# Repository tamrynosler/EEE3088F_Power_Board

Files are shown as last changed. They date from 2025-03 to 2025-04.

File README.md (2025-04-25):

# Micro-Mouse Design Project - KiCad Files

## 📖 Overview
This repository contains documentation, schematics, and PCB files used during the design of the Micro-Mouse Power Board.
There were a few issues with our original KiCad file getting corrupted so we had to copy its contents into a new KiCad project file.

## 📁 Important Files

The most recent and completed version of the project files can be found along the following file path:
- `Power Board/EEE3088F Power Board/NEW_KICAD` – Main KiCad project files (schematic, PCB, BOM etc...)

This 'NEW_KICAD' folder contains:
- Project files (schematic and PCB)
- Imported footprint and symbol files
- Production Files in `Power Board/EEE3088F Power Board/NEW_KICAD/jlcpcb/production_files` (BOM, CPL, GERBER files)
- A few other 3D Model and library files we made trying to import random things (Please forgive us if this is a mess, most of the importing was done at 3am ;) )

## 👥 Authors

- Tamryn Osler; OSLTAM001 (@tamrynosler)
- Glen Jones; JNSGLE007 (@githubusername)

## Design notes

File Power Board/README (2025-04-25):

This Repo contains the KiCad files associated with a UCT EEE3088F micro-mouse power subsystem design.

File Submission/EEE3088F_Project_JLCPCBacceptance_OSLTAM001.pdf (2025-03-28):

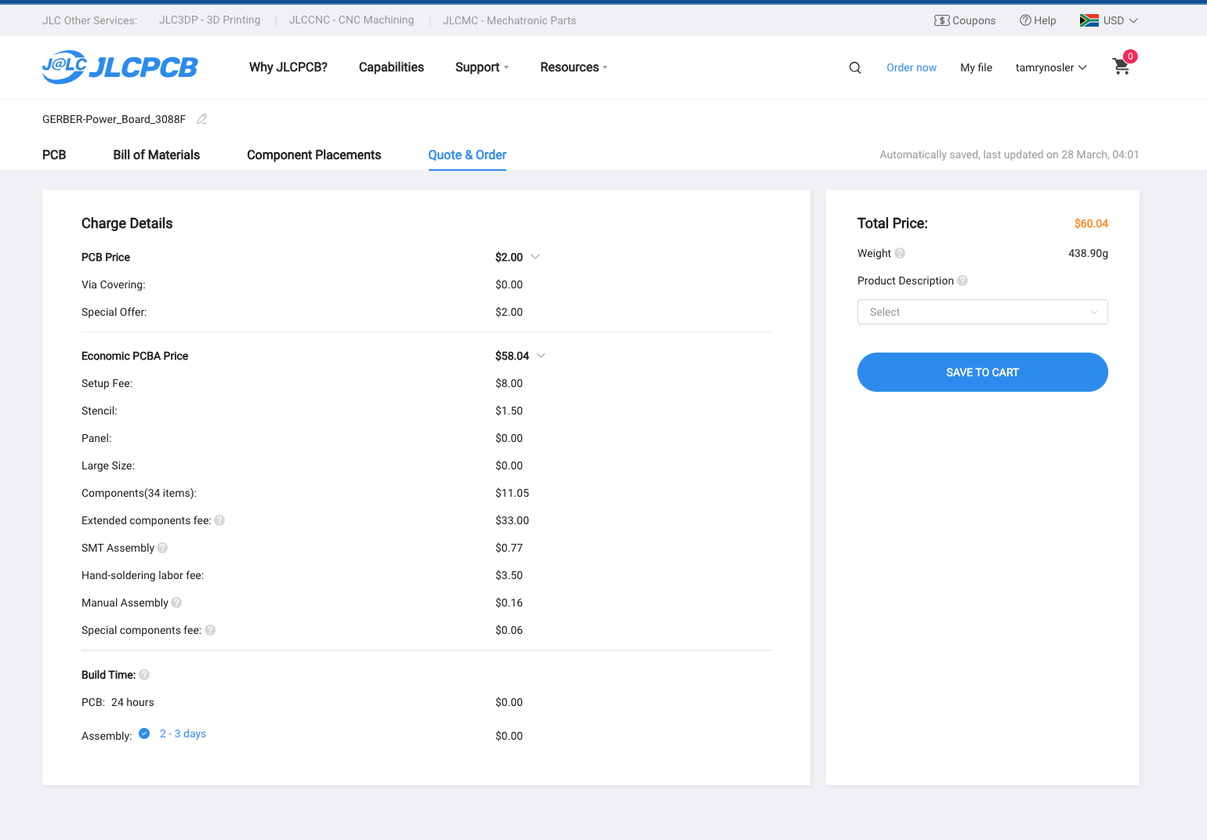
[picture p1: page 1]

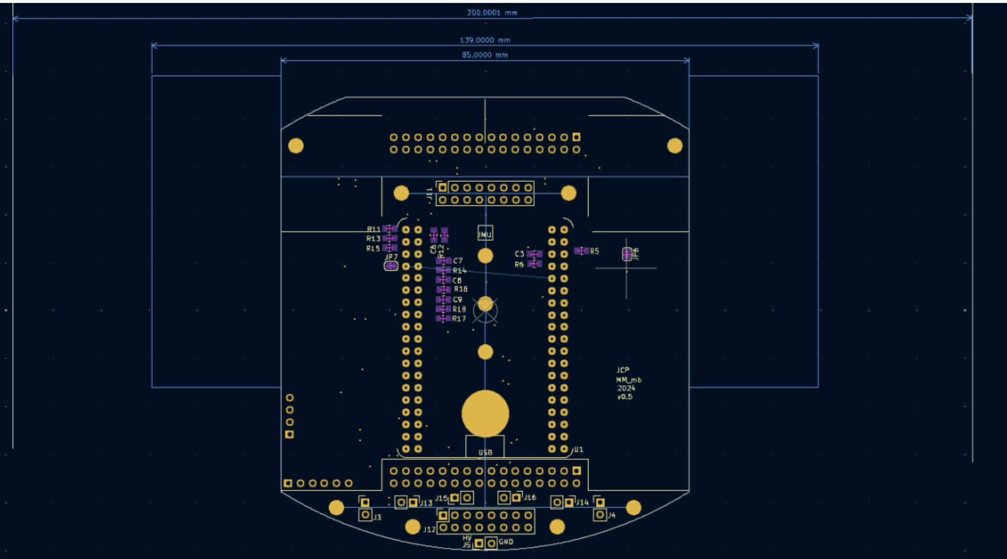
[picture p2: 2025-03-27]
Power Board/EEE3088F Power Board/NEW_KICAD/Reference board pic.jpg

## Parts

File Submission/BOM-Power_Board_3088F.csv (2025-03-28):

Comment | Designator | Footprint | LCSC | Quantity
2k7 | R_Bfast1 | R_0603_1608Metric_Pad0.98x0.95mm_HandSolder | C13167 | 1
10uF | C_B1 | C_1206_3216Metric_Pad1.33x1.80mm_HandSolder | C13585 | 1
1uF | C_C1,C_L1,C_L2 | C_0603_1608Metric_Pad1.08x0.95mm_HandSolder | C15849 | 3
1n | C_L3,C_L4 | C_0603_1608Metric_Pad1.08x0.95mm_HandSolder | C1588 | 2
TP4056-42-ESOP8 | U6 | SOIC127P600X175-9N | C16581 | 1
18uH | LB1 | L_Abracon_ASPI-4030S | C167882 | 1
220uF | C_B4 | CP_Elec_6.3x7.7 | C19100600 | 1
1k | R_B3,R_B4,R_C2,R_P1,R_P2 | R_0603_1608Metric_Pad0.98x0.95mm_HandSolder | C21190 | 5
100R | R_B6 | R_0603_1608Metric_Pad0.98x0.95mm_HandSolder | C22775 | 1
LED__P1 | 5V0,D4 | LED_0603_1608Metric_Pad1.05x0.95mm_HandSolder | C2286 | 2
LED_P2 | 3V3,D8 | LED_0603_1608Metric_Pad1.05x0.95mm_HandSolder | C2290 | 2
1R | R21,R22 | R_0603_1608Metric_Pad0.98x0.95mm_HandSolder | C22936 | 2
3k3 | R_B2,R_I1,R_I2 | R_0603_1608Metric_Pad0.98x0.95mm_HandSolder | C22978 | 3
5k6 | R_Bslow2 | R_0603_1608Metric_Pad0.98x0.95mm_HandSolder | C23189 | 1
510k | R_Pfb1 | R_0603_1608Metric_Pad0.98x0.95mm_HandSolder | C23192 | 1
6k8 | R_C3 | R_0603_1608Metric_Pad0.98x0.95mm_HandSolder | C23212 | 1
68k | R_Pfb2 | R_0603_1608Metric_Pad0.98x0.95mm_HandSolder | C23231 | 1
10k | R_B1,R_B7,R_C1 | R_0603_1608Metric_Pad0.98x0.95mm_HandSolder | C25804 | 3
~ | U4 | USB-C-SMD_G-SWITCH_GT-USB-7010ASV | C2988369 | 1
1uH | L_P3 | L_Changjiang_FXL0630 | C3040349 | 1
DRV8837DSGR | U14,U15,U16,U17 | SON50P200X200X80-9N | C39159 | 4
AP22966DC8-7 | U7 | IC_AP22966DC8-7 | C441830 | 1
10nF | C_B2 | C_0603_1608Metric_Pad1.08x0.95mm_HandSolder | C57112 | 1
22u | C_P2,C_P3,C_P4,C_P6 | C_0603_1608Metric_Pad1.08x0.95mm_HandSolder | C59461 | 4
AMS1117-3.3 | U_P2 | SOT-223-3_TabPin2 | C6186 | 1
BA340A | D7 | B340A | C64982 | 1
~ | SW1 | SW-TH_SS-12D11G5 | C692484 | 1
0.1 | R_SH1 | R_1206_3216Metric_Pad1.30x1.75mm_HandSolder | C7467250 | 1
2N7002 | Q2 | SOT-23 | C8545 | 1
INA219AxDCN | U2 | SOT-23-8 | C87469 | 1
TPS61022 | U_P1 | Texas_RWU0007A_VQFN-7_2x2mm_P0.5mm | C915088 | 1
10uF | C_B3,C_B5,C_P1,C_P5 | C_0603_1608Metric_Pad1.08x0.95mm_HandSolder | C96446 | 4
CH224K | U9 | SSOP-10-1EP_3.9x4.9mm_P1mm_EP2.1x3.3mm | C970725 | 1
TPS5430DDA | U5 | SOIC-8-1EP_3.9x4.9mm_P1.27mm_EP2.29x3mm | C9864 | 1

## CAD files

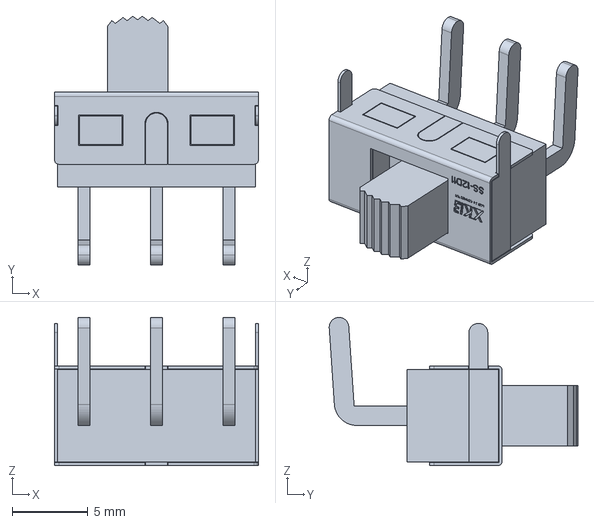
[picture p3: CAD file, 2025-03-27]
Power Board/EEE3088F Power Board/NEW_KICAD/3D_MODEL/ss-12d11g5.igs
13.5 x 16.4 x 9.80 mm

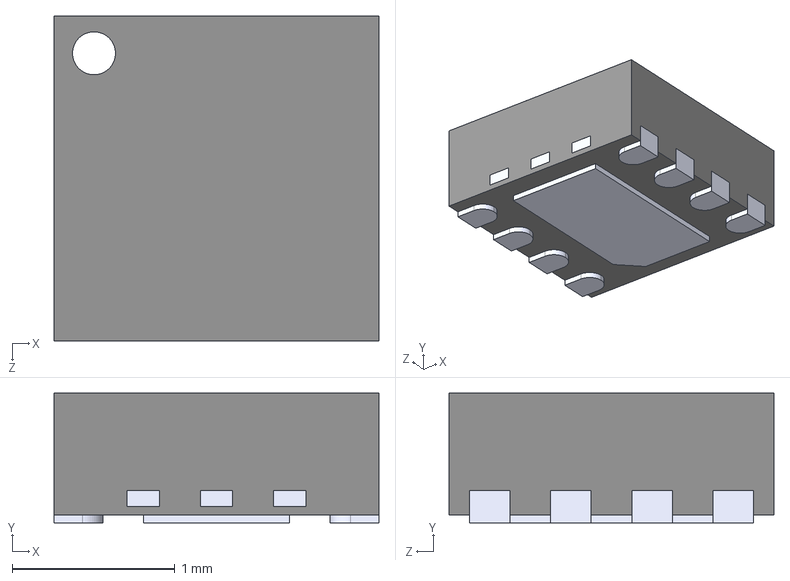
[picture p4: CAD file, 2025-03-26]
Power Board/EEE3088F Power Board/NEW_KICAD/3D_MODEL/DRV8837DSGR.step
2.00 x 0.8 x 2.00 mm

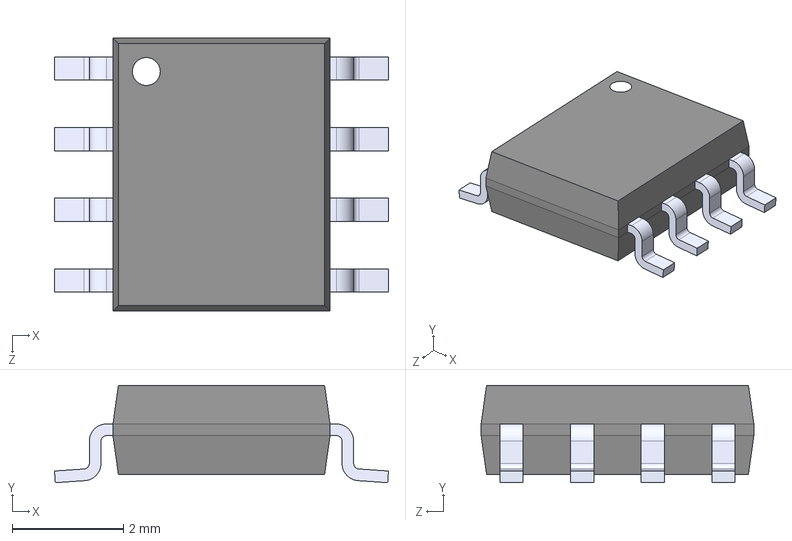
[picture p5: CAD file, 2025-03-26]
Power Board/EEE3088F Power Board/NEW_KICAD/3D_MODEL/TP4056-42-ESOP8.step
6.00 x 1.75 x 4.90 mm

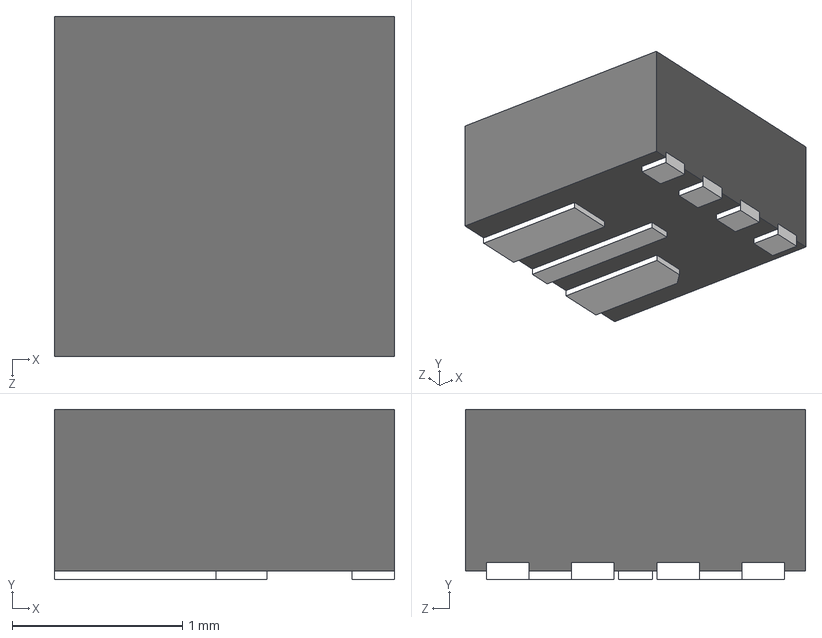
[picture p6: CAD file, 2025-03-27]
Power Board/EEE3088F Power Board/NEW_KICAD/3D_MODEL/TPS61022RWUR.stp
2.00 x 1.00 x 2.00 mm

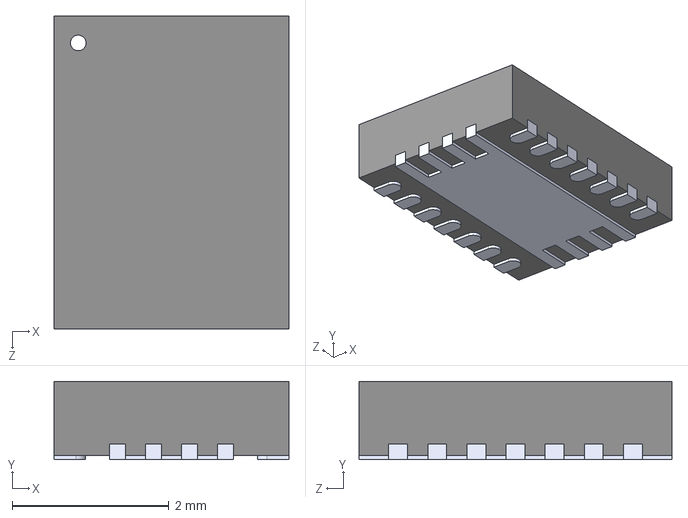
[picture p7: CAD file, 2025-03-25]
Power Board/Imported_Files/TPS63020DSJR/TPS63020DSJR.step
3.00 x 1.00 x 4.00 mm

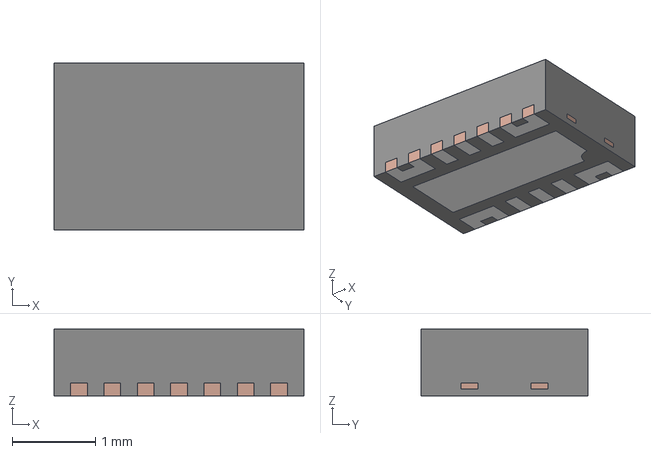
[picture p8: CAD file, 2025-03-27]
Power Board/EEE3088F Power Board/NEW_KICAD/3D_MODEL/AP22966DC8-7.stp
3.00 x 2.00 x 0.8 mm
CPD
LDF

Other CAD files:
Power Board/EEE3088F Power Board/NEW_KICAD/3D_MODEL/ss-12d11g5.stl

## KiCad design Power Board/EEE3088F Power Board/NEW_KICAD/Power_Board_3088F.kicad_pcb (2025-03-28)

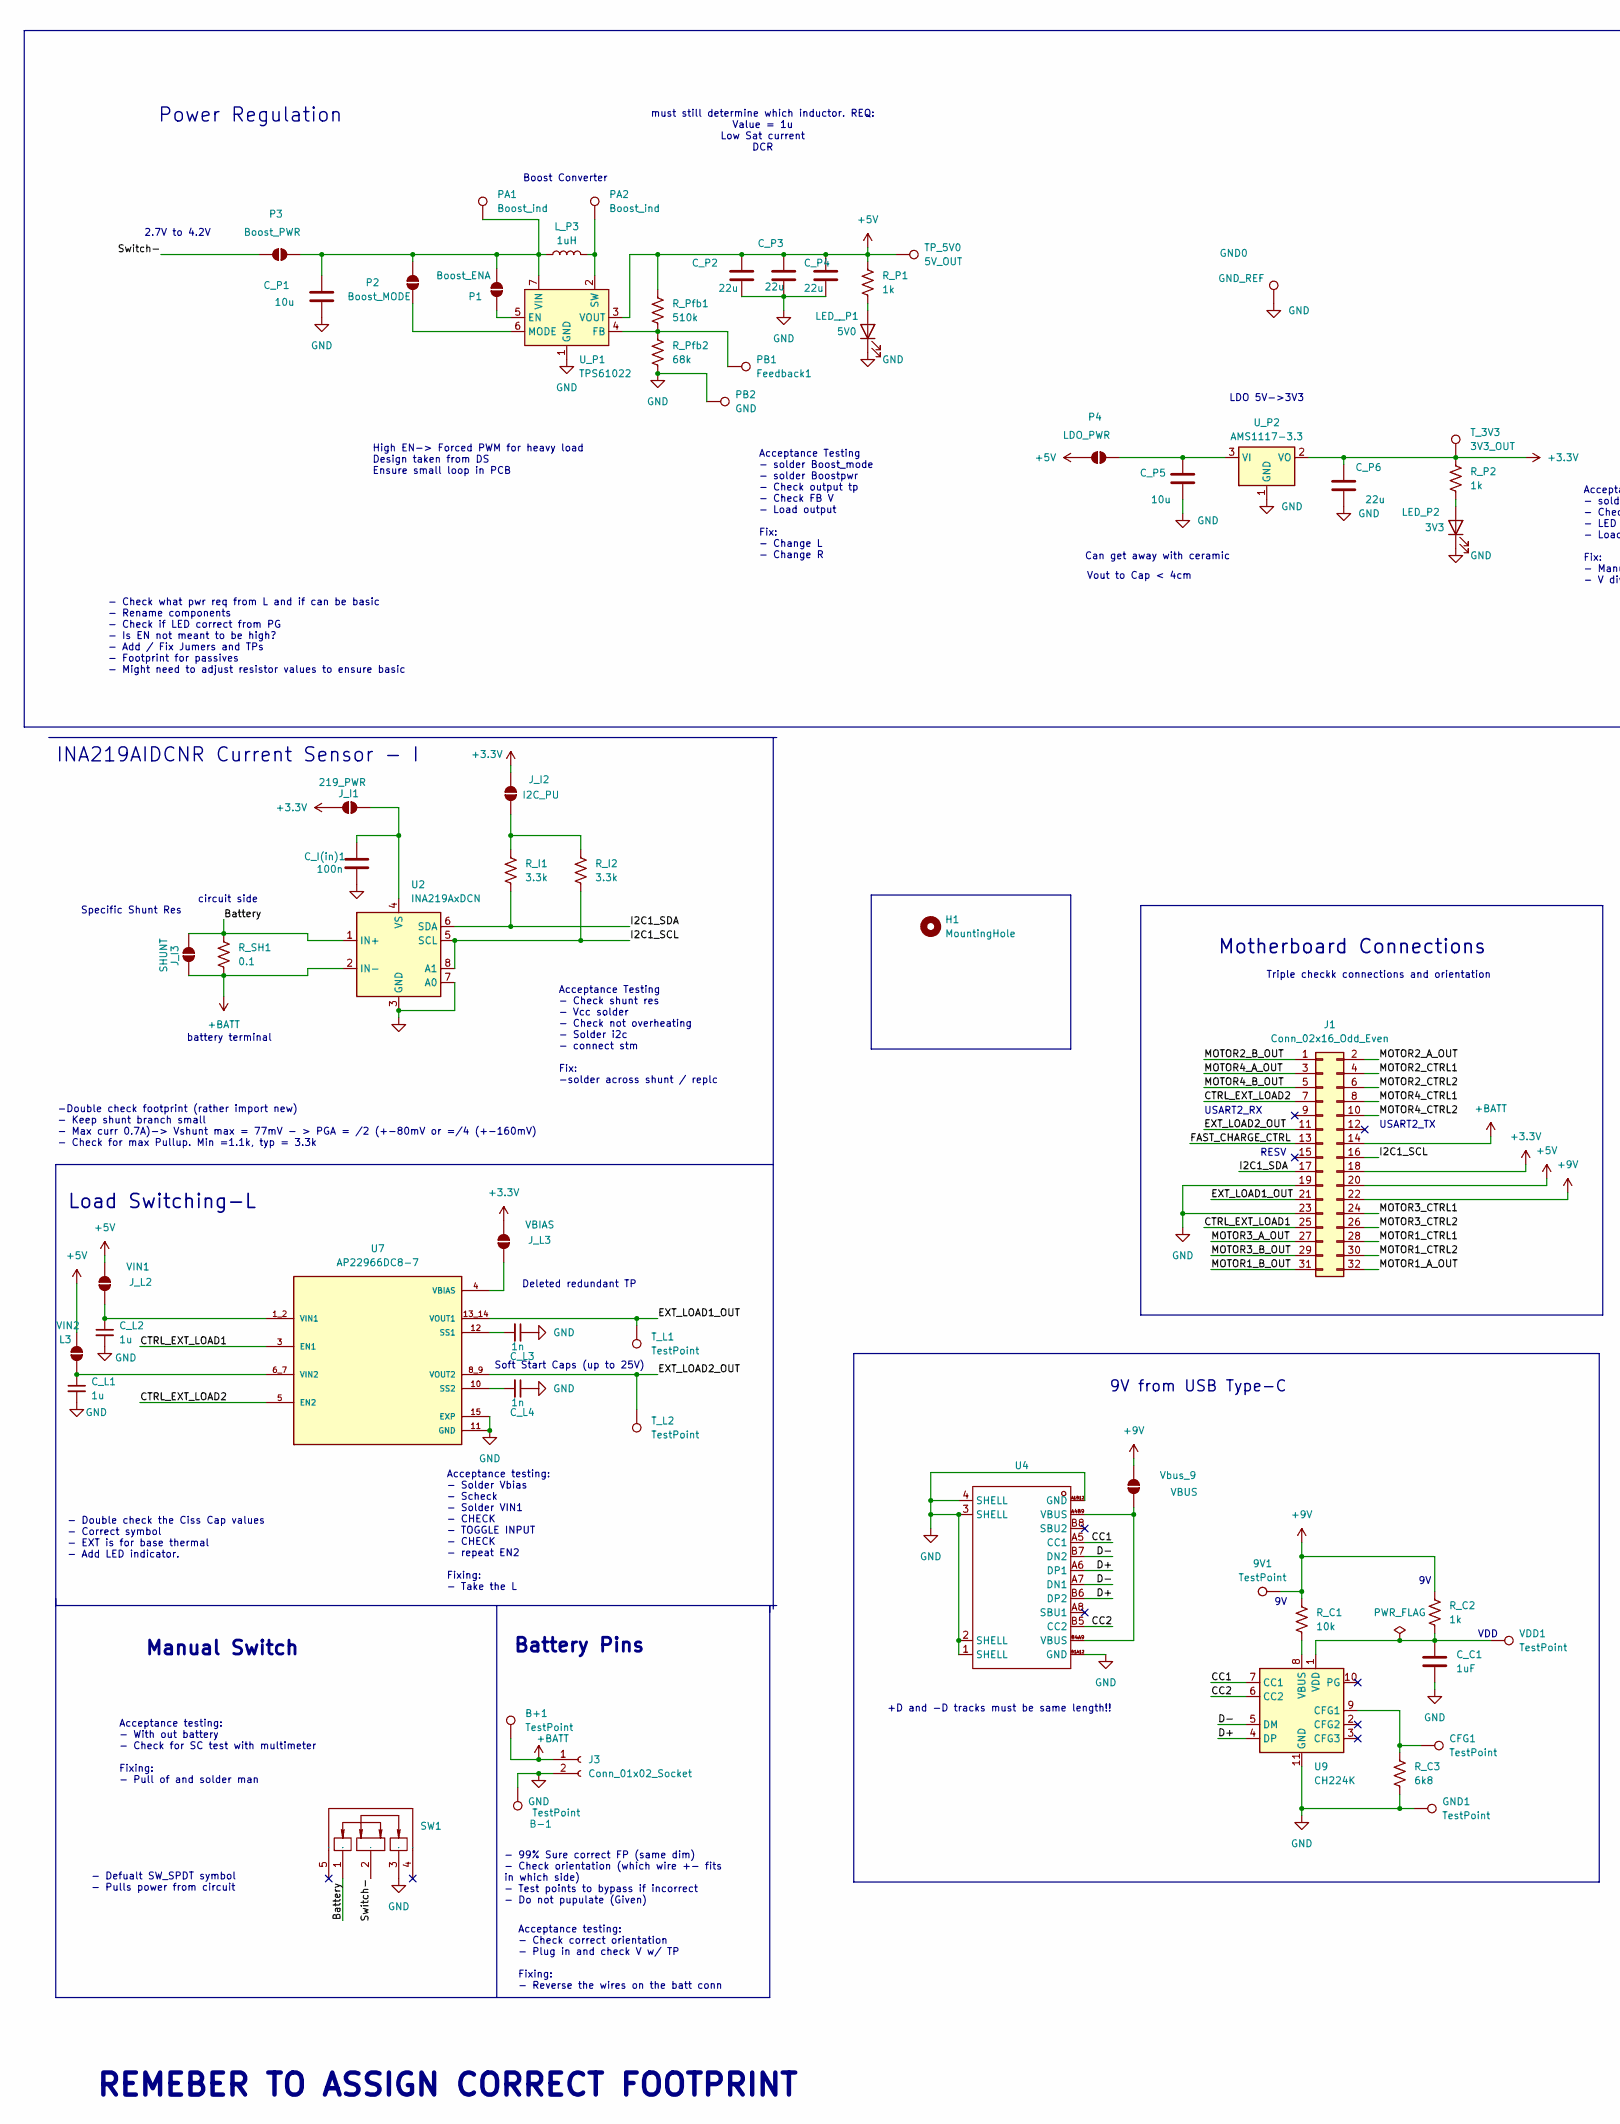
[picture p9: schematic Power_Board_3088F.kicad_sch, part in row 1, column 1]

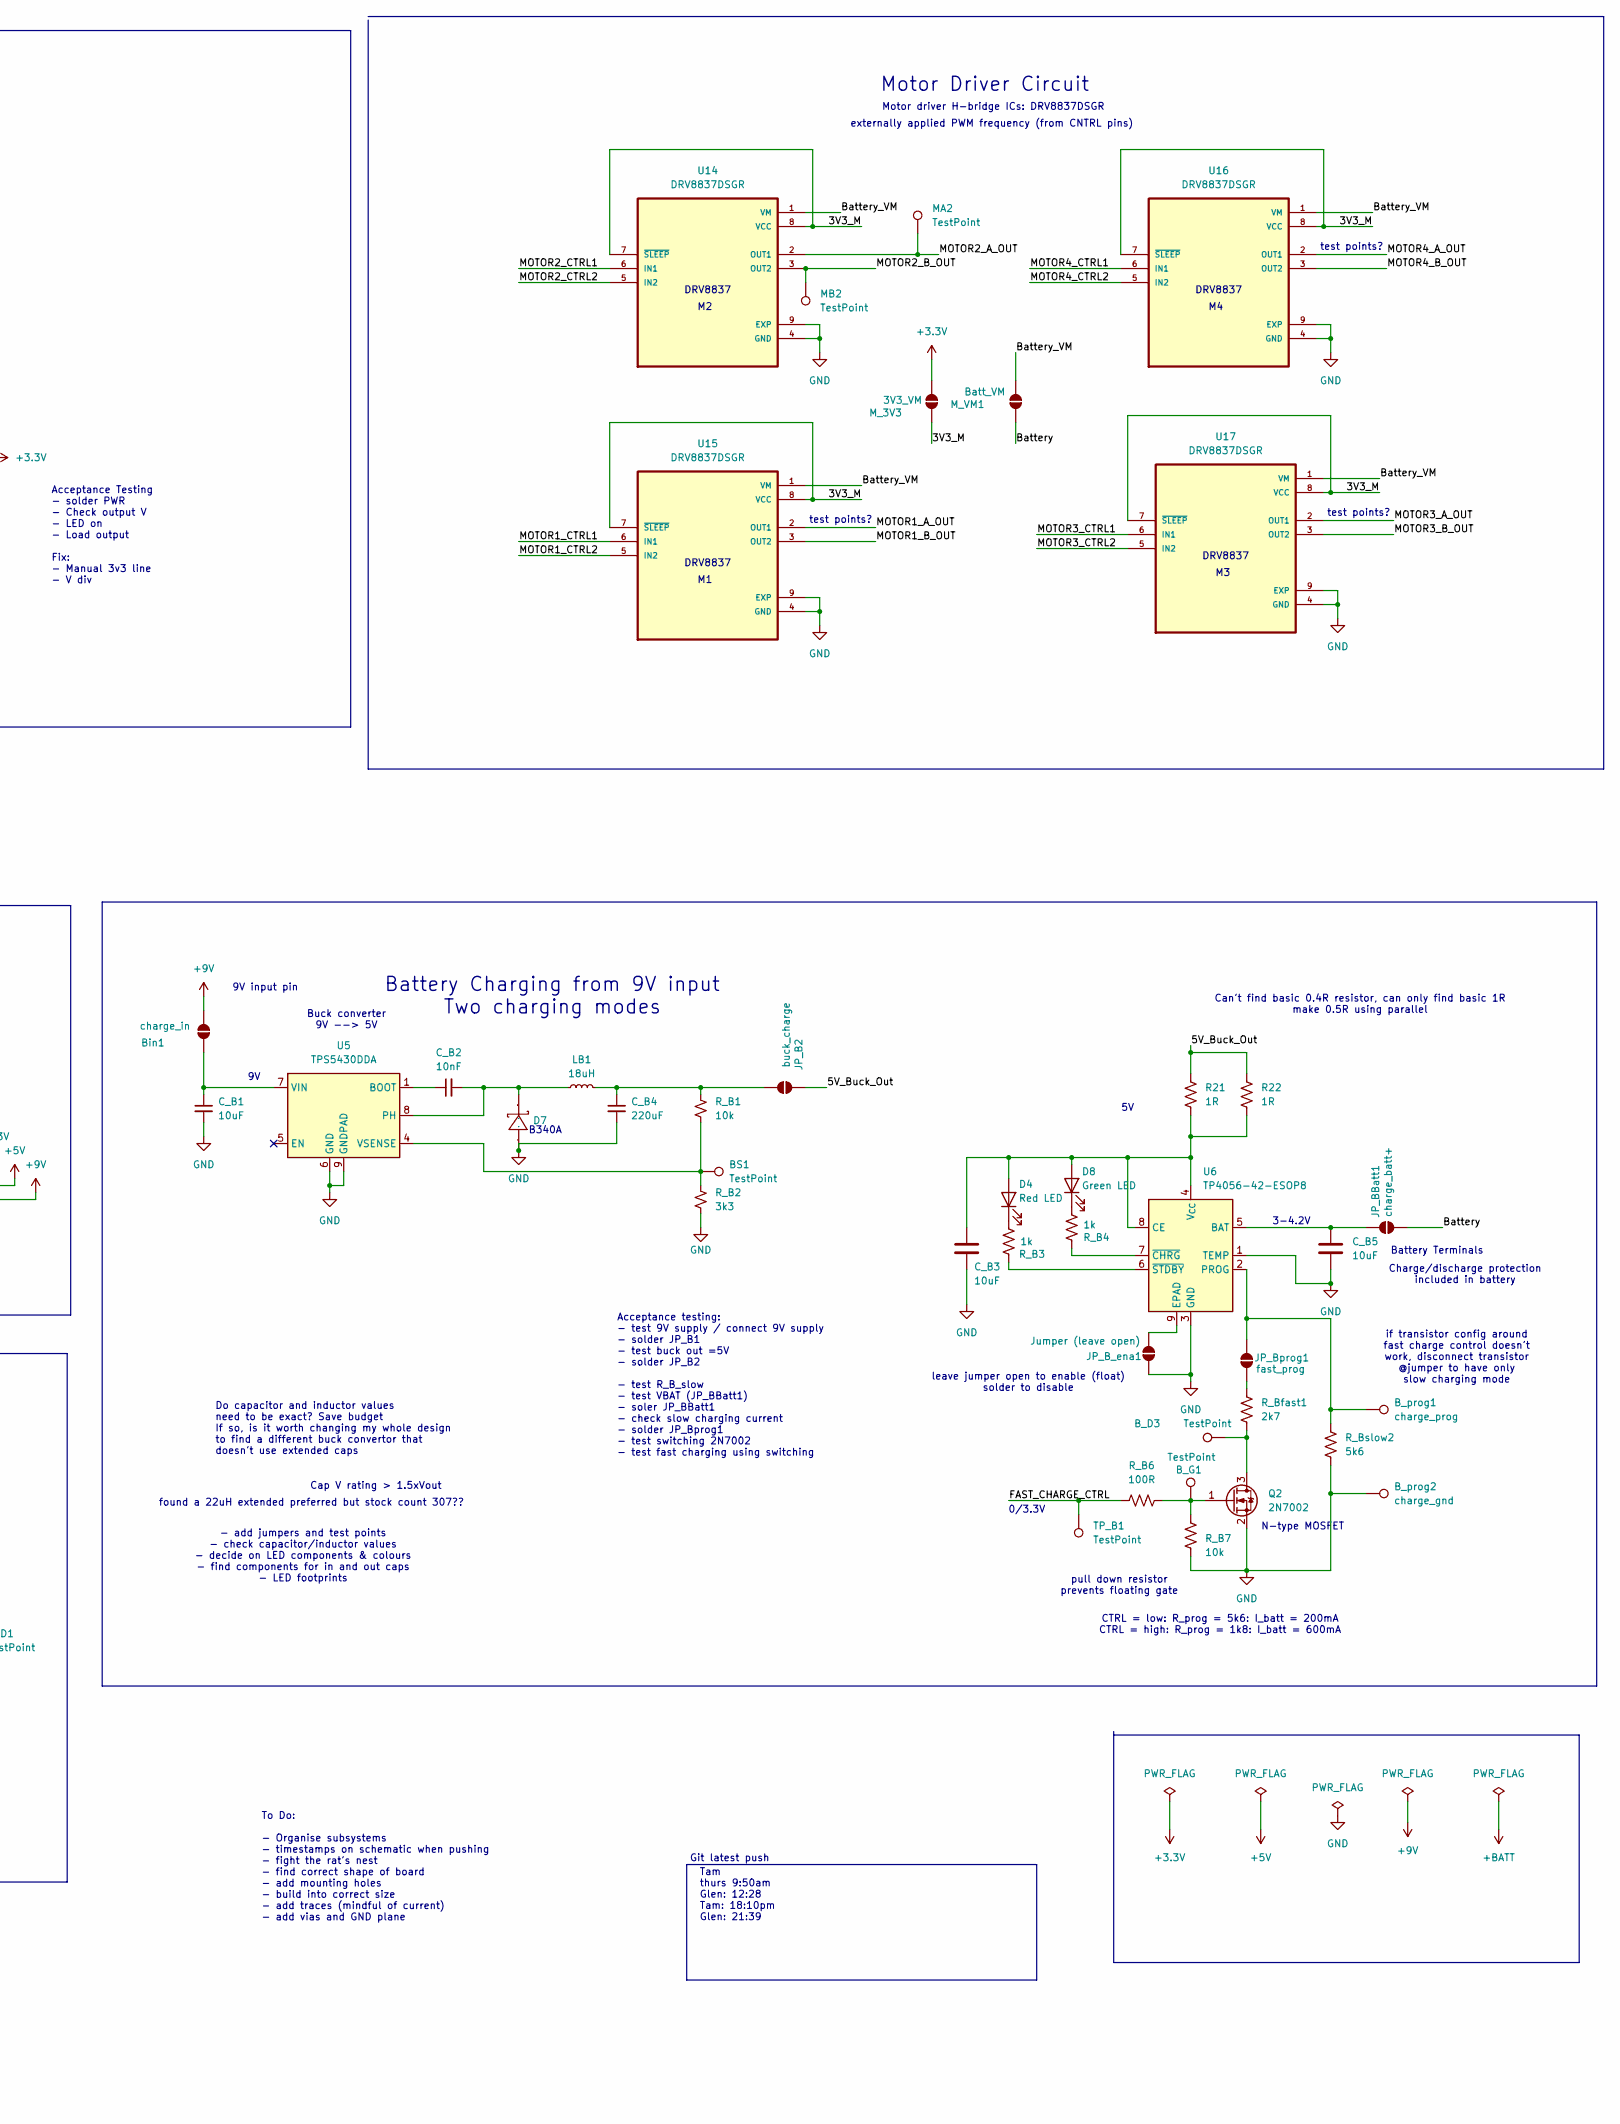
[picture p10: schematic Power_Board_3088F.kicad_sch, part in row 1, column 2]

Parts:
3V3: LED_P2; LED_0603_1608Metric_Pad1.05x0.95mm_HandSolder
5V0: LED__P1; LED_0603_1608Metric_Pad1.05x0.95mm_HandSolder
9V1: TestPoint; TestPoint_Pad_D2.0mm
B+1: TestPoint; TestPoint_Pad_D2.0mm
B-1: TestPoint; TestPoint_Pad_D2.0mm
BS1: TestPoint; TestPoint_Pad_D2.0mm
B_D3: TestPoint; TestPoint_Pad_D2.0mm
B_G1: TestPoint; TestPoint_Pad_D2.0mm
B_prog1: charge_prog; TestPoint_Pad_D2.0mm
B_prog2: charge_gnd; TestPoint_Pad_D2.0mm
Bin1: charge_in; SolderJumper-2_P1.3mm_Open_RoundedPad1.0x1.5mm
CFG1: TestPoint; TestPoint_Pad_D2.0mm
C_B1: 10uF; C_1206_3216Metric_Pad1.33x1.80mm_HandSolder
C_B2: 10nF; C_0603_1608Metric_Pad1.08x0.95mm_HandSolder
C_B3, C_B5: 10uF; C_0603_1608Metric_Pad1.08x0.95mm_HandSolder
C_B4: 220uF; CP_Elec_6.3x7.7
C_C1: 1uF; C_0603_1608Metric_Pad1.08x0.95mm_HandSolder
C_I(in)1: 100n; C_0603_1608Metric_Pad1.08x0.95mm_HandSolder
C_L1, C_L2: 1u; C_0603_1608Metric_Pad1.08x0.95mm_HandSolder
C_L3, C_L4: 1n; C_0603_1608Metric_Pad1.08x0.95mm_HandSolder
C_P1, C_P5: 10u; C_0603_1608Metric_Pad1.08x0.95mm_HandSolder
C_P2, C_P3, C_P4, C_P6: 22u; C_0603_1608Metric_Pad1.08x0.95mm_HandSolder
D4: Red LED; LED_0603_1608Metric_Pad1.05x0.95mm_HandSolder; JLCPCB Part # C2286
D7: BA340A; B340A; Manufacturer Part B340A; LCSC Part Name 电压:40V 电流:3A
D8: Green LED; LED_0603_1608Metric_Pad1.05x0.95mm_HandSolder; JLCPCB Part # C2297
GND0: GND_REF; TestPoint_Pad_D2.0mm
GND1: TestPoint; TestPoint_Pad_D2.0mm
H1: MountingHole; MountingHole_3.2mm_M3
J1: Conn_02x16_Odd_Even; PinHeader_2x16_P2.54mm_Vertical
J3: Conn_01x02_Socket; JST_PH_S2B-PH-K_1x02_P2.00mm_Horizontal
JP_B2: buck_charge; SolderJumper-2_P1.3mm_Open_RoundedPad1.0x1.5mm
JP_BBatt1: charge_batt+; SolderJumper-2_P1.3mm_Open_RoundedPad1.0x1.5mm
JP_B_ena1: Jumper (leave open); SolderJumper-2_P1.3mm_Open_RoundedPad1.0x1.5mm
JP_Bprog1: fast_prog; SolderJumper-2_P1.3mm_Open_RoundedPad1.0x1.5mm
J_I1: 219_PWR; SolderJumper-2_P1.3mm_Open_RoundedPad1.0x1.5mm
J_I2: I2C_PU; SolderJumper-2_P1.3mm_Open_RoundedPad1.0x1.5mm
J_I3: SHUNT; SolderJumper-2_P1.3mm_Open_RoundedPad1.0x1.5mm
J_L2: VIN1; SolderJumper-2_P1.3mm_Open_RoundedPad1.0x1.5mm
J_L3: VBIAS; SolderJumper-2_P1.3mm_Open_RoundedPad1.0x1.5mm
L3: VIN2; SolderJumper-2_P1.3mm_Open_RoundedPad1.0x1.5mm
LB1: 18uH; L_Abracon_ASPI-4030S
L_P3: 1uH; L_Changjiang_FXL0630
MA2: TestPoint; TestPoint_Pad_D2.0mm
MB2: TestPoint; TestPoint_Pad_D2.0mm
M_3V3: 3V3_VM; SolderJumper-2_P1.3mm_Open_RoundedPad1.0x1.5mm
M_VM1: Batt_VM; SolderJumper-2_P1.3mm_Open_RoundedPad1.0x1.5mm
P1: Boost_ENA; SolderJumper-2_P1.3mm_Open_RoundedPad1.0x1.5mm
P2: Boost_MODE; SolderJumper-2_P1.3mm_Open_RoundedPad1.0x1.5mm
P3: Boost_PWR; SolderJumper-2_P1.3mm_Open_RoundedPad1.0x1.5mm
P4: LDO_PWR; SolderJumper-2_P1.3mm_Open_RoundedPad1.0x1.5mm
PA1, PA2: Boost_ind; TestPoint_Pad_D2.0mm
PB1: Feedback1; TestPoint_Pad_D2.0mm
PB2: GND; TestPoint_Pad_D2.0mm
Q2: 2N7002; SOT-23
R21, R22: 1R; R_0603_1608Metric_Pad0.98x0.95mm_HandSolder
R_B1, R_B7: 10k; R_0603_1608Metric_Pad0.98x0.95mm_HandSolder
R_B2: 3k3; R_0603_1608Metric_Pad0.98x0.95mm_HandSolder
R_B3, R_B4: 1k; R_0603_1608Metric_Pad0.98x0.95mm_HandSolder
R_B6: 100R; R_0603_1608Metric_Pad0.98x0.95mm_HandSolder
R_Bfast1: 2k7; R_0603_1608Metric_Pad0.98x0.95mm_HandSolder
R_Bslow2: 5k6; R_0603_1608Metric_Pad0.98x0.95mm_HandSolder
R_C1: 10k; R_0603_1608Metric_Pad0.98x0.95mm_HandSolder
R_C2: 1k; R_0603_1608Metric_Pad0.98x0.95mm_HandSolder
R_C3: 6k8; R_0603_1608Metric_Pad0.98x0.95mm_HandSolder
R_I1, R_I2: 3.3k; R_0603_1608Metric_Pad0.98x0.95mm_HandSolder
R_P1, R_P2: 1k; R_0603_1608Metric_Pad0.98x0.95mm_HandSolder
R_Pfb1: 510k; R_0603_1608Metric_Pad0.98x0.95mm_HandSolder
R_Pfb2: 68k; R_0603_1608Metric_Pad0.98x0.95mm_HandSolder
R_SH1: 0.1; R_1206_3216Metric_Pad1.30x1.75mm_HandSolder
SW1: SW-TH_SS-12D11G5; Manufacturer Part SS-12D11G5; LCSC Part Name 柄长5mm 弯插双档 滑动开关
TP_5V0: 5V_OUT; TestPoint_Pad_D2.0mm
TP_B1: TestPoint; TestPoint_Pad_D2.0mm
T_3V3: 3V3_OUT; TestPoint_Pad_D2.0mm
T_L1, T_L2: TestPoint; TestPoint_Pad_D2.0mm
U2: INA219AxDCN; SOT-23-8
U4: USB-C-SMD_G-SWITCH_GT-USB-7010ASV; Manufacturer Part GT-USB-7010ASV; LCSC Part Name Type-C 母 卧贴
U5: TPS5430DDA; SOIC-8-1EP_3.9x4.9mm_P1.27mm_EP2.29x3mm
U6: TP4056-42-ESOP8; SOIC127P600X175-9N
U7: AP22966DC8-7; IC_AP22966DC8-7; PARTREV 3-2
U9: CH224K; SSOP-10-1EP_3.9x4.9mm_P1mm_EP2.1x3.3mm
U14, U15, U16, U17: DRV8837DSGR; SON50P200X200X80-9N; DigiKey_Part_Number 296-34806-2-ND
U_P1: TPS61022; Texas_RWU0007A_VQFN-7_2x2mm_P0.5mm
U_P2: AMS1117-3.3; SOT-223-3_TabPin2
VDD1: TestPoint; TestPoint_Pad_D2.0mm
Vbus_9: VBUS; SolderJumper-2_P1.3mm_Open_RoundedPad1.0x1.5mm

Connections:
+3.3V: C_P6.2, J1.18, J_I1.1 (A), J_I2.1 (A), J_L3.2 (B), M_3V3.2 (B), R_P2.1, T_3V3.1, U_P2.2 (VO)
+5V: C_P2.2, C_P3.2, C_P4.2, J1.20, J_L2.2 (B), L3.2 (B), P4.2 (B), R_P1.1, R_Pfb1.1, TP_5V0.1, U_P1.3 (VOUT)
+9V: 9V1.1, Bin1.2 (B), J1.22, R_C1.1, R_C2.1, Vbus_9.1 (A)
+BATT: B+1.1, J1.14, J3.1, J_I3.1 (A), R_SH1.2, U2.2 (IN-)
/3V3_M: M_3V3.1 (A), U14.7 (~SLEEP), U14.8 (VCC), U15.7 (~SLEEP), U15.8 (VCC), U16.7 (~SLEEP), U16.8 (VCC), U17.7 (~SLEEP), U17.8 (VCC)
/5V_Buck_Out: JP_B2.1 (A), R21.1, R22.1
/Battery: JP_BBatt1.2 (B), J_I3.2 (B), M_VM1.1 (A), R_SH1.1, SW1.1, U2.1 (IN+)
/Battery_VM: M_VM1.2 (B), U14.1 (VM), U15.1 (VM), U16.1 (VM), U17.1 (VM)
/CC1: U4.A5 (CC1), U9.7 (CC1)
/CC2: U4.B5 (CC2), U9.6 (CC2)
/CTRL_EXT_LOAD1: J1.25, U7.3 (EN1)
/CTRL_EXT_LOAD2: J1.7, U7.5 (EN2)
/D+: U4.A6 (DP1), U4.B6 (DP2), U9.4 (DP)
/D-: U4.A7 (DN1), U4.B7 (DN2), U9.5 (DM)
/EXT_LOAD1_OUT: J1.21, T_L1.1, U7.13_14 (VOUT1)
/EXT_LOAD2_OUT: J1.11, T_L2.1, U7.8_9 (VOUT2)
/FAST_CHARGE_CTRL: J1.13, R_B6.1, TP_B1.1
/I2C1_SCL: J1.16, R_I2.2, U2.5 (SCL), U2.8 (A1)
/I2C1_SDA: J1.17, R_I1.2, U2.6 (SDA)
/MOTOR1_A_OUT: J1.32, U15.2 (OUT1)
/MOTOR1_B_OUT: J1.31, U15.3 (OUT2)
/MOTOR1_CTRL1: J1.28, U15.6 (IN1)
/MOTOR1_CTRL2: J1.30, U15.5 (IN2)
/MOTOR2_A_OUT: J1.2, MA2.1, U14.2 (OUT1)
/MOTOR2_B_OUT: J1.1, MB2.1, U14.3 (OUT2)
/MOTOR2_CTRL1: J1.4, U14.6 (IN1)
/MOTOR2_CTRL2: J1.6, U14.5 (IN2)
/MOTOR3_A_OUT: J1.27, U17.2 (OUT1)
/MOTOR3_B_OUT: J1.29, U17.3 (OUT2)
/MOTOR3_CTRL1: J1.24, U17.6 (IN1)
/MOTOR3_CTRL2: J1.26, U17.5 (IN2)
/MOTOR4_A_OUT: J1.3, U16.2 (OUT1)
/MOTOR4_B_OUT: J1.5, U16.3 (OUT2)
/MOTOR4_CTRL1: J1.8, U16.6 (IN1)
/MOTOR4_CTRL2: J1.10, U16.5 (IN2)
/Switch-: P3.2 (B), SW1.2
<NO NET>: C_I(in)1.1, U2.3 (GND), U2.7 (A0)
GND: 3V3.1 (K), 5V0.1 (K), B-1.1, B_prog2.1, C_B1.2, C_B3.2, C_B4.2, C_B5.2, C_C1.2, C_L1.2, C_L2.2, C_L3.1, C_L4.1, C_P1.1, C_P2.1, C_P3.1, C_P4.1, C_P5.1, C_P6.1, D7.2 (A), GND0.1, GND1.1, J1.19, J1.23, J3.2, JP_B_ena1.1 (A), PB2.1, Q2.2 (S), R_B2.2, R_B7.2, R_Bslow2.2, R_C3.2, R_Pfb2.2, SW1.3, U4.1 (SHELL), U4.2 (SHELL), U4.3 (SHELL), U4.4 (SHELL), U4.A1B12 (GND), U4.B1A12 (GND), U5.6 (GND), U5.9 (GNDPAD), U6.1 (TEMP), U6.3 (GND), U7.11 (GND), U7.15 (EXP), U9.11 (GND), U14.4 (GND), U14.9 (EXP), U15.4 (GND), U15.9 (EXP), U16.4 (GND), U16.9 (EXP), U17.4 (GND), U17.9 (EXP), U_P1.1 (GND), U_P2.1 (GND)
unnamed: 3V3.2 (A), R_P2.2
unnamed: 5V0.2 (A), R_P1.2
unnamed: Bin1.1 (A), C_B1.1, U5.7 (VIN)
unnamed: C_B3.1, D4.2 (A), D8.2 (A), R21.2, R22.2, U6.4 (V_{CC}), U6.8 (CE)
unnamed: D4.1 (K), R_B3.1
unnamed: C_B2.2, D7.1 (K), LB1.1, U5.8 (PH)
unnamed: D8.1 (K), R_B4.1
unnamed: C_B4.1, JP_B2.2 (B), LB1.2, R_B1.1
unnamed: C_B5.1, JP_BBatt1.1 (A), U6.5 (BAT)
unnamed: JP_B_ena1.2 (B), U6.9 (EPAD)
unnamed: B_prog1.1, JP_Bprog1.1 (A), R_Bslow2.1, U6.2 (PROG)
unnamed: JP_Bprog1.2 (B), R_Bfast1.1
unnamed: C_I(in)1.2, J_I1.2 (B), U2.4 (VS)
unnamed: J_I2.2 (B), R_I1.1, R_I2.1
unnamed: C_L2.1, J_L2.1 (A), U7.1_2 (VIN1)
unnamed: J_L3.1 (A), U7.4 (VBIAS)
unnamed: C_L1.1, L3.1 (A), U7.6_7 (VIN2)
unnamed: C_P1.2, L_P3.1, P1.1 (A), P2.2 (B), P3.1 (A), PA1.1, U_P1.7 (VIN)
unnamed: P1.2 (B), U_P1.5 (EN)
unnamed: P2.1 (A), U_P1.6 (MODE)
unnamed: C_P5.2, P4.1 (A), U_P2.3 (VI)
unnamed: B_D3.1, Q2.3 (D), R_Bfast1.2
unnamed: B_G1.1, Q2.1 (G), R_B6.2, R_B7.1
unnamed: C_B2.1, U5.1 (BOOT)
unnamed: BS1.1, R_B1.2, R_B2.1, U5.4 (VSENSE)
unnamed: R_B4.2, U6.7 (~CHRG)
unnamed: R_B3.2, U6.6 (~STDBY)
unnamed: C_L3.2, U7.12 (SS1)
unnamed: C_L4.2, U7.10 (SS2)
unnamed: CFG1.1, R_C3.1, U9.9 (CFG1)
unnamed: R_C1.2, U9.8 (VBUS)
unnamed: C_C1.1, R_C2.2, U9.1 (VDD), VDD1.1
unnamed: PB1.1, R_Pfb1.2, R_Pfb2.1, U_P1.4 (FB)
unnamed: L_P3.2, PA2.1, U_P1.2 (SW)
unnamed: U4.A4B9 (VBUS), U4.B4A9 (VBUS), Vbus_9.2 (B)

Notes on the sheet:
found a 22uH extended preferred but stock count 307??
3-4.2V
REMEBER TO ASSIGN CORRECT FOOTPRINT
test points?
if transistor config around fast charge control doesn't work, disconnect transistor @jumper to have only slow charging mode
Acceptance testing: - test 9V supply / connect 9V supply - solder JP_B1 - test buck out =5V - solder JP_B2 - test R_B_slow - test VBAT (JP_BBatt1) - soler JP_BBatt1 - check slow charging current - solder JP_Bprog1 - test switching 2N7002 - test fast charging using switching
0/3.3V
DRV8837
Battery Charging from 9V input Two charging modes
High EN-> Forced PWM for heavy load Design taken from DS Ensure small loop in PCB
USART2_RX
Manual Switch
Load Switching-L
-Double check footprint (rather import new) - Keep shunt branch small - Max curr 0.7A)-> Vshunt max = 77mV - > PGA = /2 (+-80mV or =/4 (+-160mV) - Check for max Pullup. Min =1.1k, typ = 3.3k
INA219AIDCNR Current Sensor - I
battery terminal
Acceptance testing: - Check correct orientation - Plug in and check V w/ TP Fixing: - Reverse the wires on the batt conn
Vout to Cap < 4cm
Motherboard Connections
N-type MOSFET
+D and -D tracks must be same length!!
Battery Terminals
Power Regulation
Deleted redundant TP
must still determine which inductor. REQ: Value = 1u Low Sat current DCR
Battery Pins
circuit side
2.7V to 4.2V
USART2_TX
- add jumpers and test points - check capacitor/inductor values - decide on LED components & colours - find components for in and out caps - LED footprints
9V from USB Type-C
9V input pin
LDO 5V->3V3
Can't find basic 0.4R resistor, can only find basic 1R make 0.5R using parallel
pull down resistor prevents floating gate
- Defualt SW_SPDT symbol - Pulls power from circuit
Acceptance Testing - solder PWR - Check output V - LED on - Load output Fix: - Manual 3v3 line - V div
B340A
RESV
Acceptance Testing - solder Boost_mode - solder Boostpwr - Check output tp - Check FB V - Load output Fix: - Change L - Change R

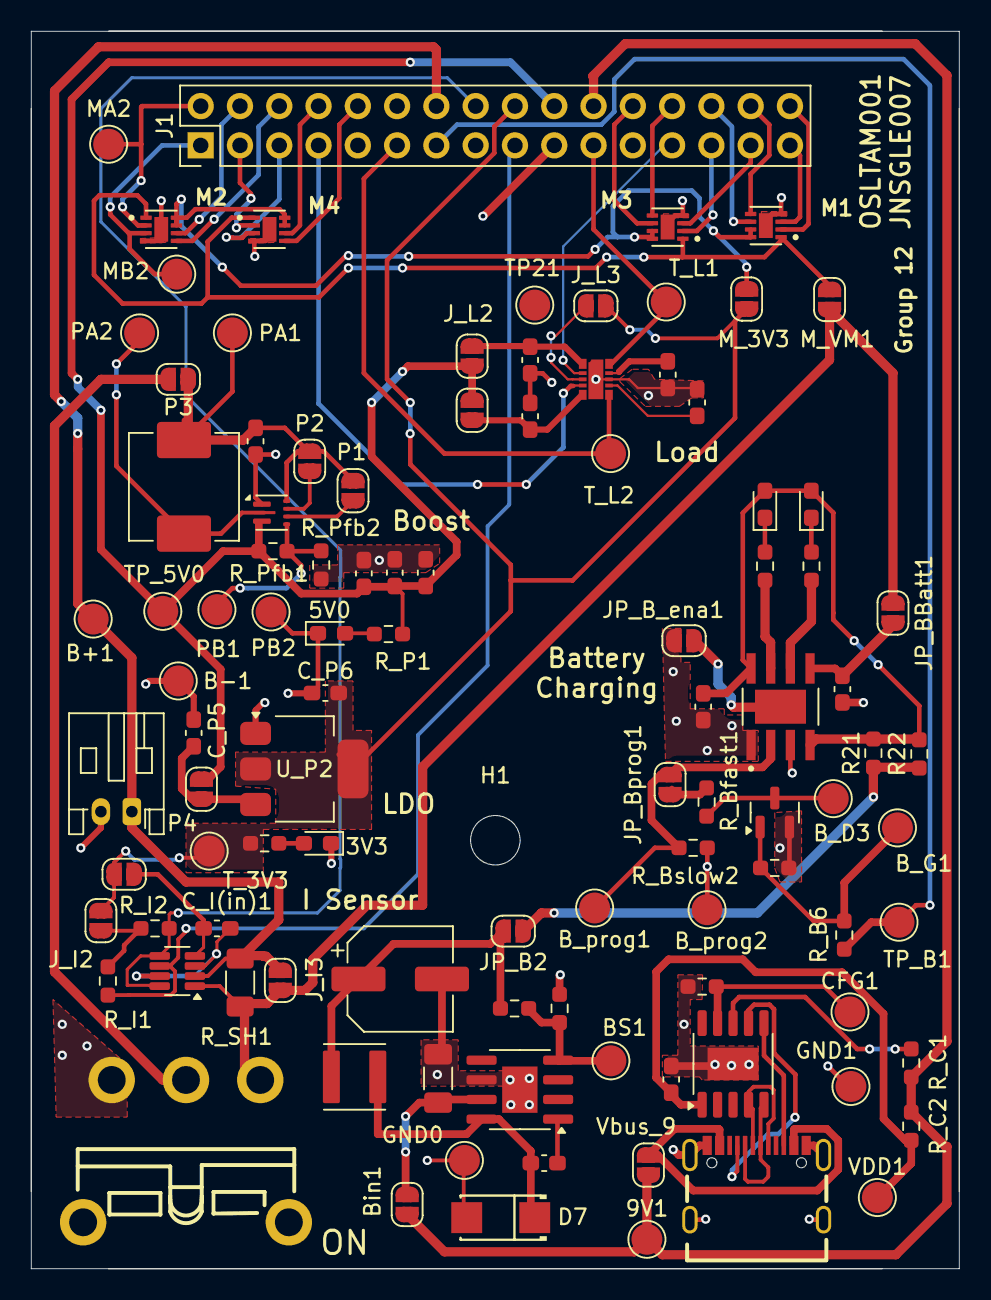
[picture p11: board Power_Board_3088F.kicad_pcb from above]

Board: 2 copper layers, 60.0 x 80.0 mm, 103 parts (0 on the bottom side), 73 nets.

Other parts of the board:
TP21: TestPoint; TestPoint_Pad_D2.0mm

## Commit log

2025-03-22 Finished INA219 and schem layout
    [EEE3088F Power Board.kicad_sch]
2025-03-22 added battery charging and started motor drivers
    [EEE3088F Power Board.kicad_sch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]
2025-03-23 Deleted EEE3088F Breadboard Design directory (unnecessary files)
    [EEE3088F Breadboard Design.kicad_pcb, EEE3088F Breadboard Design.kicad_sch]
2025-03-23 Deleted Power Board Personal directory (unnecessary files)
    [CPL-Power Board Personal.csv, Power Board Personal-CuBottom.gbr, Power Board Personal-CuTop.gbr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]
2025-03-23 finished motor driver circuit
    [EEE3088F Power Board.kicad_sch]
2025-03-23 3v3 and some footprints complete
    [EEE3088F Power Board.kicad_sch]
2025-03-23 Finished USB Type-C, added test points
    [EEE3088F Power Board.kicad_sch]
2025-03-24 Basic schematic finished
    [EEE3088F Power Board.kicad_sch]
2025-03-24 annotations, test points
    [EEE3088F Power Board.kicad_sch]
2025-03-24 checked FP PWR reg and Curr Sens
    [EEE3088F Power Board.kicad_sch]
2025-03-24 IC and passive component footprints added
    [EEE3088F Power Board.kicad_sch]
2025-03-25 more labels and footprints
    [EEE3088F Power Board.kicad_sch]
2025-03-25 notes and checked. SW FP to o
    [EEE3088F Power Board.kicad_sch]
2025-03-25 added footprints and fixed buck
    [EEE3088F Power Board.kicad_sch]
2025-03-25 Added com file
    [TPS63020DSJR.step]
2025-03-26 Fixed communal fp and symbols
    [EEE3088F Power Board.kicad_sch]
2025-03-26 ELC checks
    [EEE3088F Power Board.kicad_sch]
2025-03-26 fixed footprints and symbols
    [EEE3088F Power Board.kicad_pcb, EEE3088F Power Board.kicad_sch]
2025-03-26 still no footprints on pcb editor (mac error)
    [EEE3088F Power Board.kicad_sch]
2025-03-26 killing the mac version
    [EEE3088F Power Board.kicad_sch]
2025-03-26 New windows Kicad ;)
    [Power_Board_3088F.kicad_pcb, Power_Board_3088F.kicad_sch]
2025-03-26 finished schematic
    [EEE3088F Power Board.kicad_sch, Power_Board_3088F.kicad_pcb, Power_Board_3088F.kicad_sch]
2025-03-26 pcb islands done
    [Power_Board_3088F.kicad_pcb, Power_Board_3088F.kicad_sch]
2025-03-27 arranged rats nest Tam
    [Power_Board_3088F.kicad_pcb, Power_Board_3088F.kicad_sch]
2025-03-27 Glen finished organising PCB & some 3D
    [AP22966DC8-7.stp, DRV8837DSGR.step, Power_Board_3088F.kicad_pcb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]
2025-03-27 traces started
    [Power_Board_3088F.kicad_pcb, Power_Board_3088F.kicad_sch]
2025-03-27 Mostly finished Schem
    [Power_Board_3088F.kicad_pcb, Power_Board_3088F.kicad_sch]
2025-03-28 final v0
    [BOM-Power_Board_3088F.csv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]

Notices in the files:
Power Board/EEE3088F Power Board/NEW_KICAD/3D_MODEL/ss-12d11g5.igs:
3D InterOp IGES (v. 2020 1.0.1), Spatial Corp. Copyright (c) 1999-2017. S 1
